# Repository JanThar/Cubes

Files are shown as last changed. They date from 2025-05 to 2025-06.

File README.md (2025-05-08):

- scad datei allgemeine datei. Wenn man di folgenden Sachen auf 1 setz kriegt man ne Aubauvorschau
  // Show lasercutted housing [0,1]
  showWall = 0;
  // Show lasercutted mechanics [0,1]
  showMechanics = 0;
  // Show 3D-printed parts [0,1]
  showPrint = 0;
  // Show axis and motors [0,1]
  showDrive = 0;
  // Show electronics [0,1]
  showElectronic = 0;
  bzw. mit // Flatten for lasercutting [0,1] flatten = 1;
  projection(cut = false) mechanics();
  oder
  projection(cut = false) walls();
  die Laserdateien und unter // 3D-printed die einzelnen 3D-Druckdateien
- svg für den laser, bei der Mechanics datei die z-achse platte und zahnstangen
  (links, zweite/dritte/vierte von oben) nicht cutten, wird vermutlich durch 3D druck ersetzt.
-  stl dateien zum drucken, Anzahl am Ende des Namens. Die 3 Toolhalter (Mill, Penholder, Laser)
  müssen noch mal überarbeitet werden (und dann zusammen mit z-Achsenplatte und Zahnstangen)

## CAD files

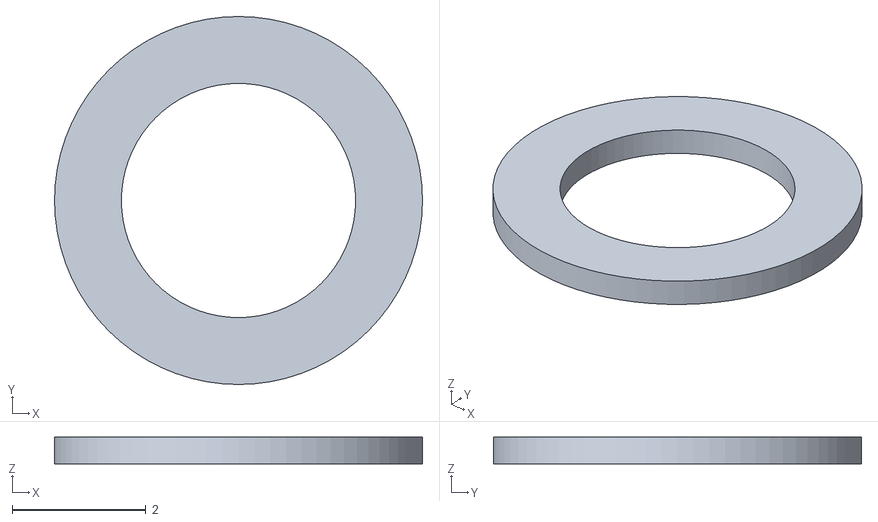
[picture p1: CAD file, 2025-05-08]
unterleg_2.stl
5.50 x 5.50 x 0.4

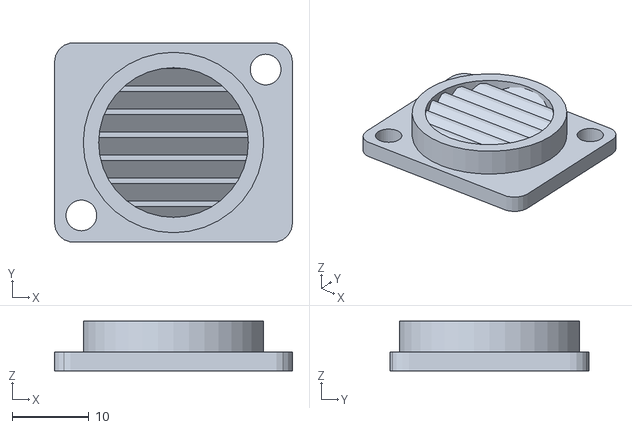
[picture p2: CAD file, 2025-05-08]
neutrixvent_1.stl
31.0 x 25.9 x 6.50

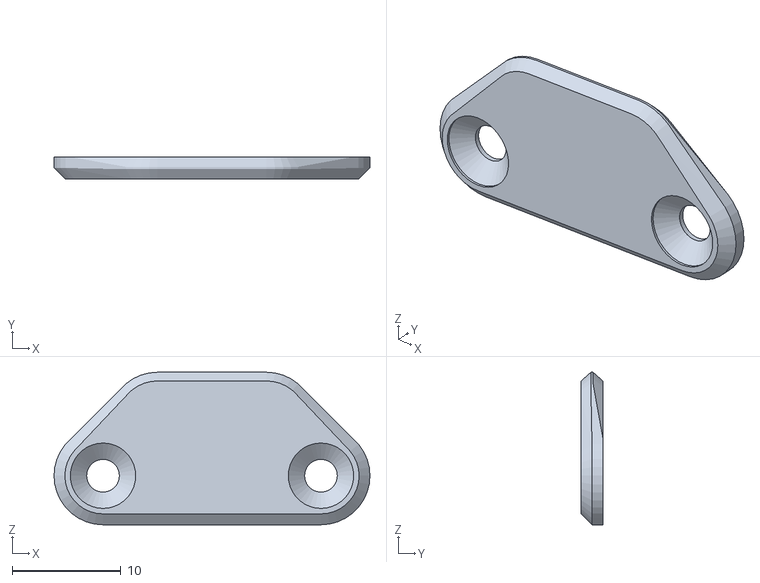
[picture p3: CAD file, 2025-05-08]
doorHandle_1.stl
29.0 x 2.00 x 14.0

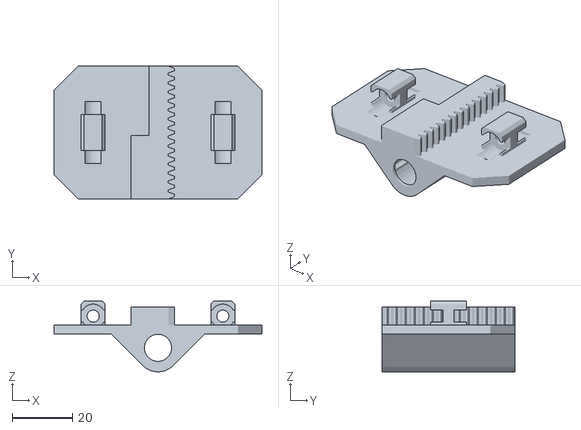
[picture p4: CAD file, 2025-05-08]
PenHolder_1_toMod.stl
69.0 x 44.0 x 23.5

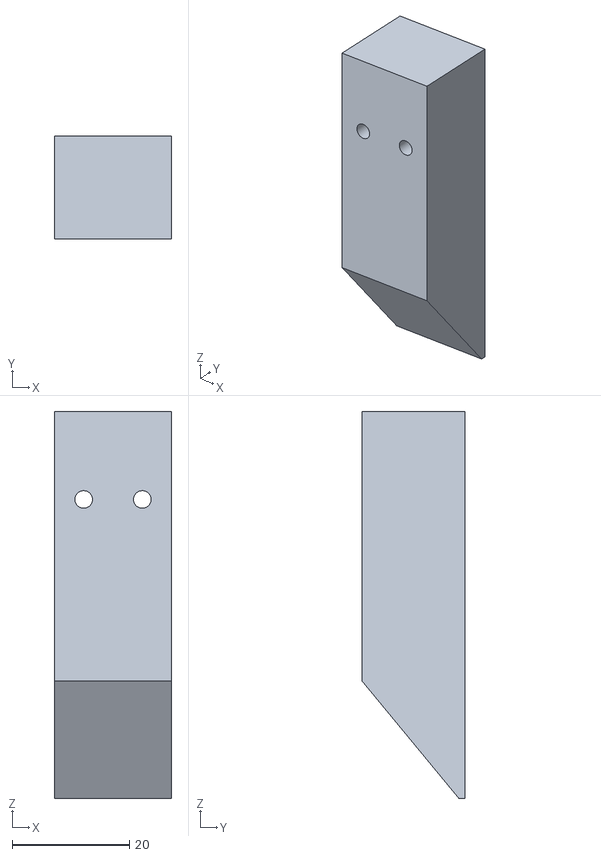
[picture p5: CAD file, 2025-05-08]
Laser_1_toMod.stl
20.0 x 17.5 x 66.0

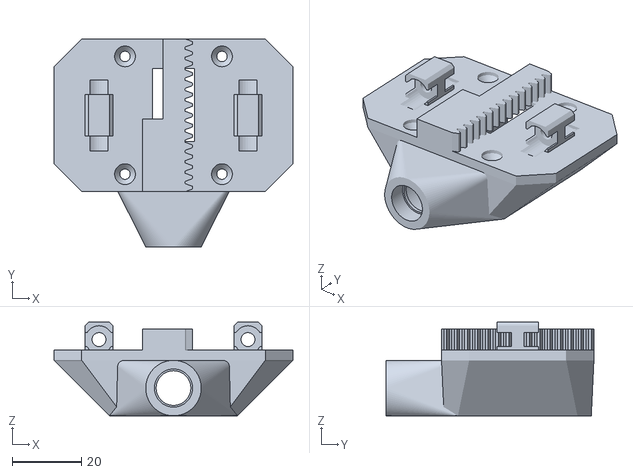
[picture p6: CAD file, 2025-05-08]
Mill_1_toMod.stl
69.0 x 60.0 x 27.0

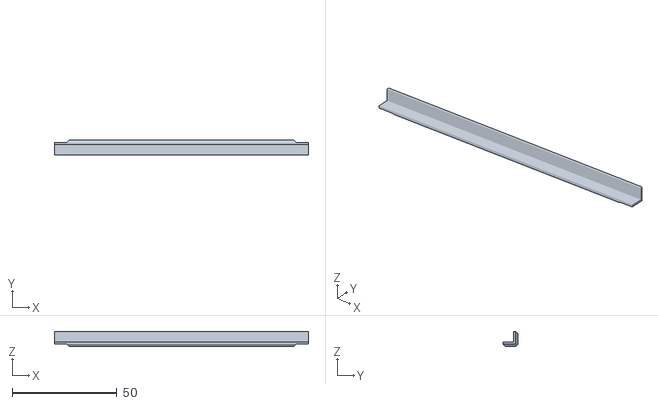
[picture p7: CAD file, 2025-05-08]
coverSide_12.stl
121.1 x 7.00 x 7.00

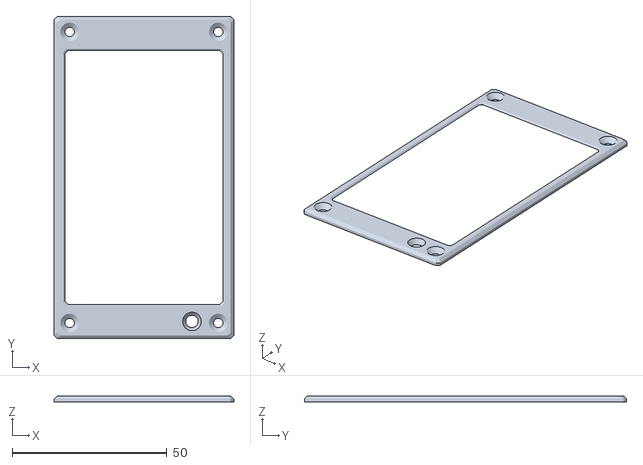
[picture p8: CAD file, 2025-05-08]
screenCover_1.stl
58.0 x 104.0 x 2.00

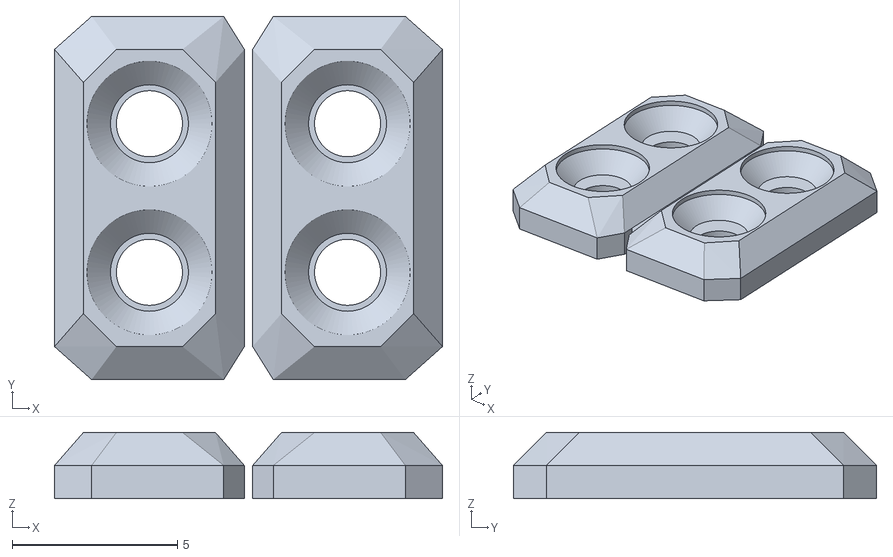
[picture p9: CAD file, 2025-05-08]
HingeA_2_comboDruck.stl
11.8 x 11.0 x 2.00

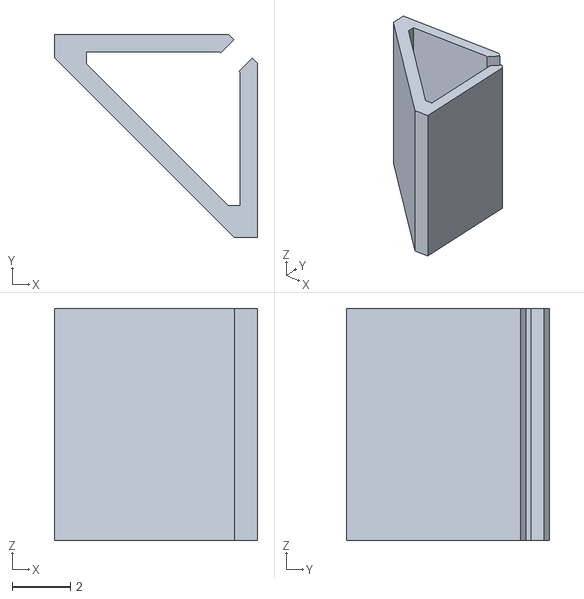
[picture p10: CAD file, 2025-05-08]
CableClip_10.stl
7.00 x 7.00 x 8.00

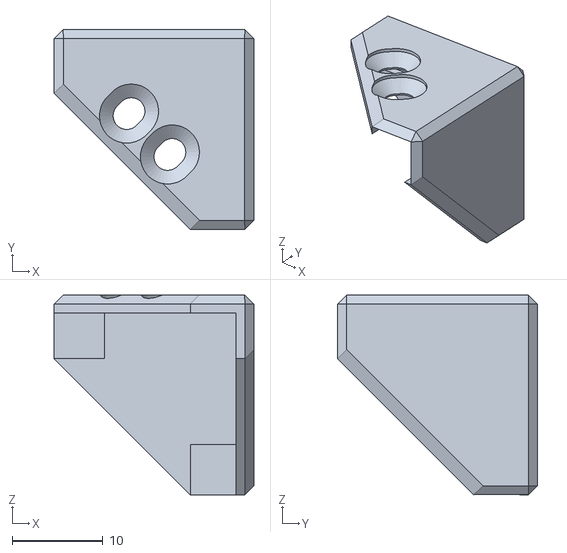
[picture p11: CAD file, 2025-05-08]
coverEdge_8.stl
22.0 x 22.0 x 22.0

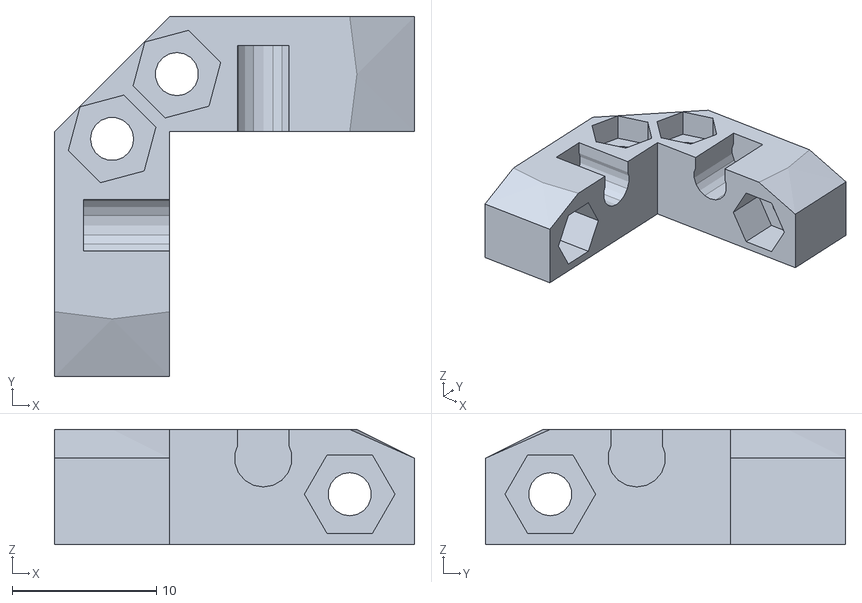
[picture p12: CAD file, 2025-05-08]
connector_30.stl
25.0 x 25.0 x 8.00

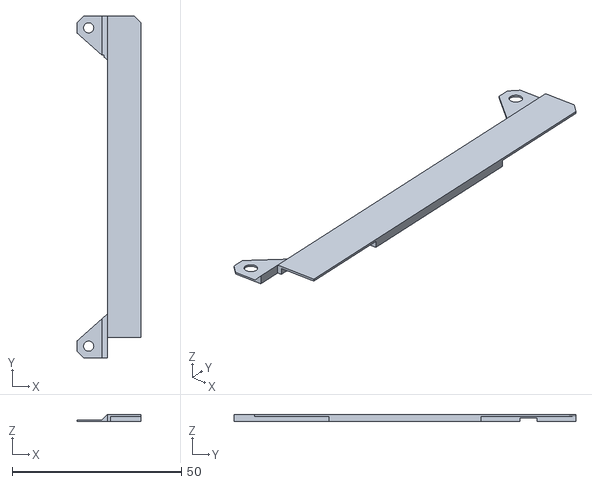
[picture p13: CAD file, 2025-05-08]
LEDHolder_1.stl
19.0 x 101.0 x 2.00

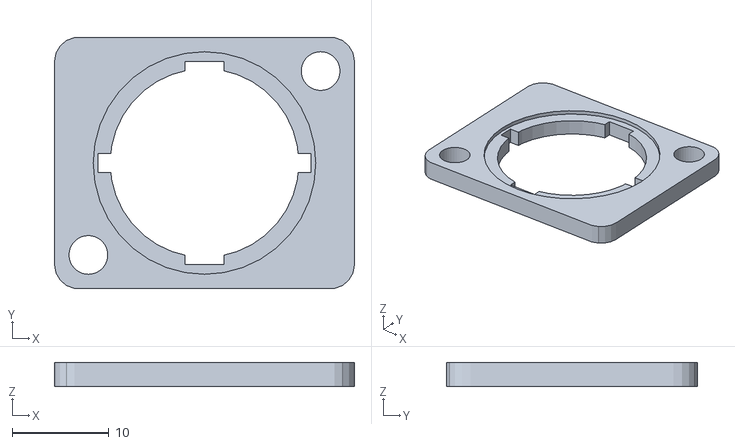
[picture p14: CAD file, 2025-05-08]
neutrixSwitch_1.stl
31.0 x 25.9 x 2.50

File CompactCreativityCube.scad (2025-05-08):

use <Getriebe.scad>

// Nur 1 Schlüsselschalter, 1 Einschalter, 2-4 Motoren!!

// ToDo 
// Türschalter: druck ausreichend??? - Position (Überlappung Neutrix)
// Tür breiter Türrahmen dünner,aussen????, scharnier durchgehend, M3
// da achse vor schlitz eventuell doch aussenrahmen (Griff/Scharnier Combo?????)

// 5 wg iMac, 3 oder 6 wegen Basisform (gelb,rot,blau,grün,lila)
// Printe/Holzmagnet:          120*4*1,5       (Laser) (Printen)
// Businesscard/Stroopwaffel:    85x55x3         (Mill) 
// Keks/Legofliese/Tattoofolie: 15.8x15.8x3.2   (Plotter)
// Marzipan                         (3D Printer)
// Sticker:                         (Cutter)
// Peppers Ghost,Waffel, Schokolade (Tiefziehen) (+Schokoladenbrunnen)
//                                  (Sticken)
// Ringegravierer??
//
// -> Aachen,Holland, Belgien als 3Eck 
//      -> !Printe,Brezel
//      -> !Belgische Waffel, Butter Crisps Blätterteigpastetchen,Pralinen,Spekulatius, Snowball
//      -> !Stroopwafels,Poffertjes

// change connector postion holes top/bottom - nuts to close to axis. add 2 instead 1

// 3D-printed stuff

// move Platform (x-Axis) [-37:37] 
positionX = -37+6;//37-25; //37-24-50
// move Tool (x-Axis) [-37:37]
positionY = 30;
// move Tool (x-Axis) [-15:15] 
positionZ = -15;//11;

// open Door [0:47]
doorAngle = 0;

// Toolhead: 0 unused, 1 Laser, 2 Mill, 3 PrintHead, 4 Pen
useTool = 4; 

toolLaser = 1;
toolMill = 2;
toolPrinter = 3;
toolPen = 4;

//gear inlay laser offset
gearAxisX = 0.12;
gearAxisY = 0.15;
gearLin   = 0.5;

//--------------------------------

positionPiOffsetX = 41;
positionPiOffsetY = 15;

// Flatten for lasercutting [0,1]
flatten = 0;
//projection(cut = false) mechanics();
//projection(cut = false) walls();

// 3D-printed 
//ledholder();
//cableClip(8);
//millInlay();
//millHolder();
//screwHead(1);
penHolder();
//cover();
//bumper();
//hingeTPU(0);
//hingePLA(0);
//doorhandle();
//screenholder(0);
//connector(0);
//vent(0);
//usbA(0);
//usbBack(0);
//keySwitch(0);
//switch(0);
//laserholder();
//wallXside(1,-1,12);

// not used anymore
//led(0);
//frameScreen(); 
//ledFrame(); 

simplifyVent=1;

explodeModules = 0;
explodeAxis = 0;
explodeHousing = 0;

printOffset = 1;//rechter Dremel : Scale 103% printOffset 1.1 (etwas zu gross) 1.05 ok

//animate
//explodeModules = 30*(1-checkA($t*3));
//explodeAxis = 150*(1-checkA($t*3-1));
//explodeHousing = 250*(1-checkA($t*3-1.8));

// Show lasercutted housing [0,1]
showWall = 0;
// Show lasercutted mechanics [0,1]
showMechanics = 0;
// Show 3D-printed parts [0,1]
showPrint = 0;
// Show axis and motors [0,1]
showDrive = 0;
// Show electronics [0,1]
showElectronic = 0;

//--------------------------------

// Dimension y
width = 144;
// Dimension x
length = 144;
// Dimension z
height = 144;
// Height z-Axis
zHeight = 75; //old: 66, new 72 bzw. 75
// Width x-Axis
xWidth = length;

// outer hull - measure for real values
hullWidth  = 150;
hullLength = 150;
hullHeight = 150;

// 139 - 139 - 67

// material thickness for lasercutted parts
materialThickness = 3;
housingThickness = 3;

penWidth = 14; // can be reduced to 12

// distance motor to border
motorDistance = 10;
// distance connectors to border
conDistance = 6;

// screw parameter
screwDiameter = 3;
screwNutDiameter = 6.3;
screwNutHeight = 2.6;
screwLength = 10;

// axis and Bearings
axisHeight = 6; //16;
axisDiameter = 4;
axisShorting = 4;
bearingDiameter = 8;
bearingLength = 8;
offsetBearing = 2.5;

// Connectors 3D-printed
conWidth = 8;
conLength = 17;
conHeight = axisHeight+axisDiameter/2;
conScrewHeight = 10;
conScrewDistance = 5;

// positions
distanceXtoBottom = 20-explodeAxis;
distanceXtoBack = 0;
distanceYtoBottom = -zHeight/2+height-conHeight*2;
distanceYtoBack = -(width/2-20)+explodeAxis;
distanceZtoBottom = distanceYtoBottom+explodeAxis;
distanceZtoBack = distanceYtoBack+32-explodeAxis;

// door parameter
doorRounding = 10;
doorOverlap = 3;
doorHeight = height-conHeight*2-distanceXtoBottom+materialThickness-15;
doorWidth = 124;
doorExtensionX = 0;
doorDistanceToBottom = distanceXtoBottom+conHeight+materialThickness+3;

//define variables to identfy axis
x=0;
y=1;
z=2;

//Animation
function checkA(a)=(checkB((a>1)?1:a));
function checkB(a)=((a<0)?0:a);

//--------------------------------

//                translate([0,-130,10]) //screen
//rotate([-70,0,0])
//                    cube([85.5,20,55],true);

//electronic
if(showElectronic) {
//    translate([length/2-positionPiOffsetX,-width/2+positionPiOffsetY,18.5]) rotate([0,180,180]) piZero(0);
    //color("green") translate([-29-8,0,10]) cube([76,121,10],center=true); // 5 inch display
}

//toolhead
if(showDrive) translate([-positionY,0,positionZ+explodeAxis]) {
    if (useTool==toolLaser) 
        translate([0,3,86-3]) {
            laser(0); // 10-100 mm Focus
            laserholder();
        }
    if (useTool==toolPen) 
        translate([0,0,86-3]) {
            //laser(0); // 10-100 mm Focus
            penHolder();
        }
    if (useTool==toolMill) 
        translate([0,-3.7,distanceZtoBottom+5]) 
        mill(); 
    if (useTool==toolPrinter) 
        translate([-6,-13-5,73+45.5-6]) 
        printhead(); 
}

//walls
if (showWall) walls();
    
//mechanic
if (showMechanics)  mechanics();
    
module cableClip(clipLength) {
    difference() {
        hull() {
            translate([0,conHeight/2-0.4,0])
                cube([conHeight-2,0.8,clipLength],true);
            translate([conHeight/2-0.4,0,0])
                cube([0.8,conHeight-2,clipLength],true);
        }
        hull() {
            translate([0.4,conHeight/2-0.4-0.4,0])
                cube([conHeight-3.4,0.4,clipLength*2],true);
            translate([conHeight/2-0.4-0.4,0.4,0])
                cube([0.4,conHeight-3.4,clipLength*2],true);
        }
        translate([3,3,0])
            rotate([0,0,-45])
            cube([0.9,conHeight-3.4,clipLength*2],true);
    }
}
    
module bumpers() {
    for(i=[0:3])
        rotate([0,0,90*i])
        bumper();
    
    for(i=[0:3])
        translate([0,0,height])
        rotate([180,0,90*i])
        bumper();
}    
module covers() {
for(i=[0:4])
    rotate([0,0,90*i])
    translate([0,0,(hullWidth-6)/2])
    rotate([0,90,0])
    cover();
translate([0,0,(hullWidth-6)/2])
    for(i=[0:4])
    rotate([90*i,0,0])
    cover();
translate([0,0,(hullWidth-6)/2])
    for(i=[0:4])
    rotate([90*i,0,90])
    cover();
}
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

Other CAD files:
neutrixUSB_A_1.stl
DoorFrame_1.stl
neutrixKey_1.stl
MillInlay_1.stl
HingeB_2_comboDruck.stl
neutrixUSB_Back_1.stl

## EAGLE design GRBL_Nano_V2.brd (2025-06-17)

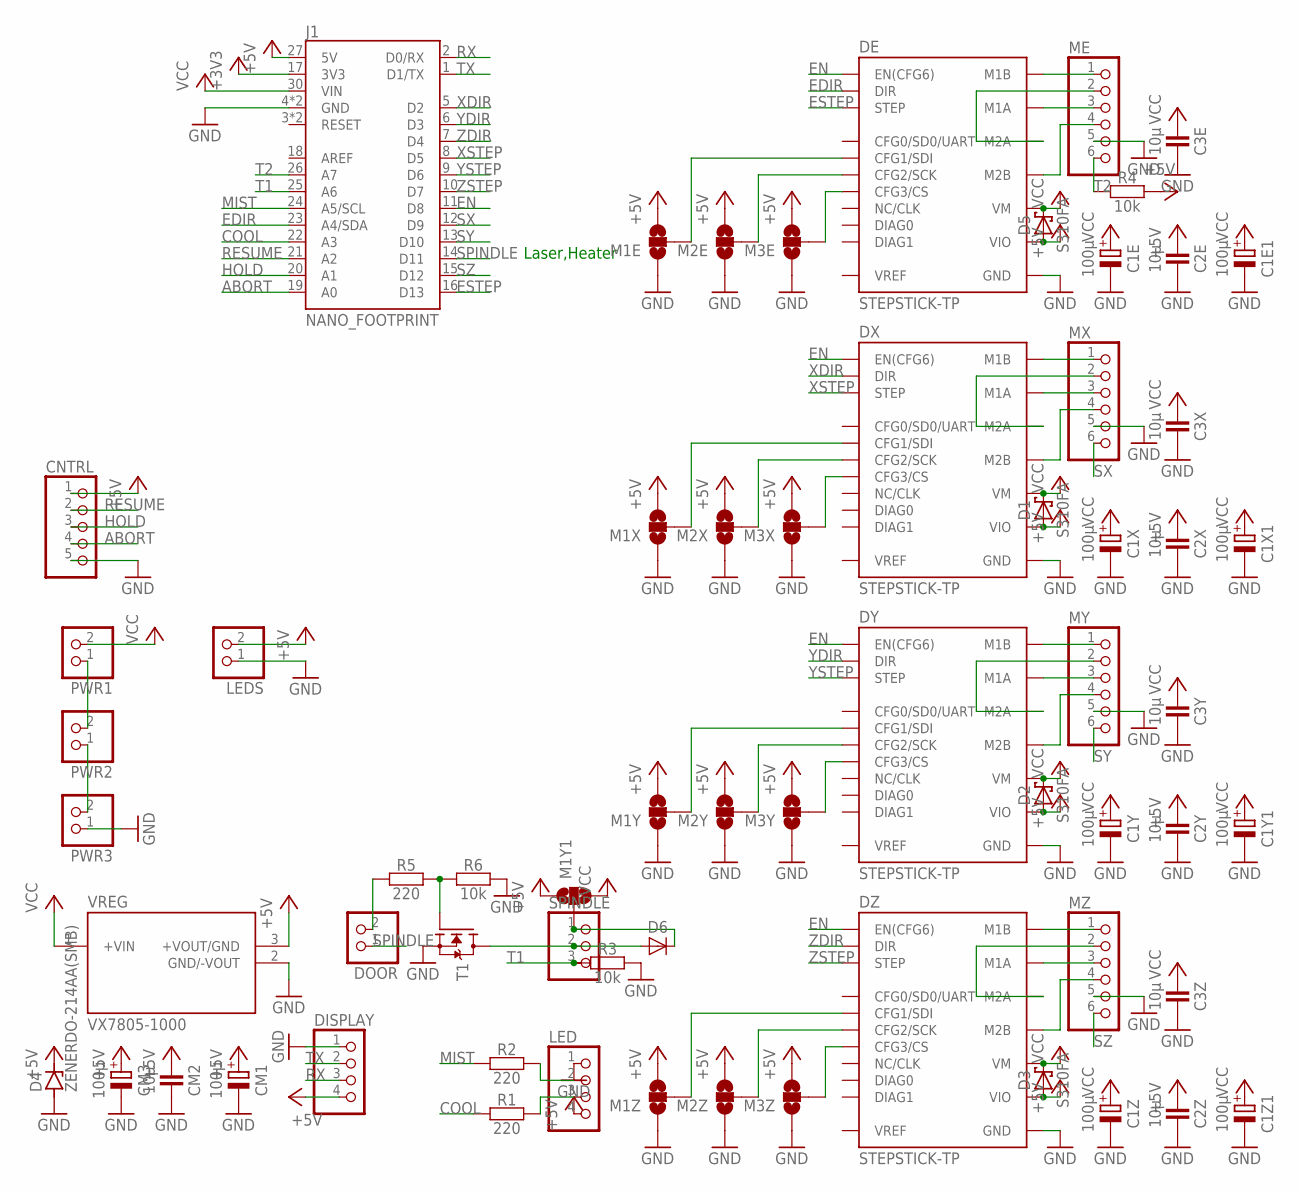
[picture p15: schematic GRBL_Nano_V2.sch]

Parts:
C1E, C1X, C1Y, C1Z: 100µ; C_8MM
C1E1, C1X1, C1Y1, C1Z1: 100µ; C_E5-10
C2E, C2X, C2Y, C2Z, C3E, C3X, C3Y, C3Z: 10µ; C0805
CM1: 100µ; C_8MM
CM2: 10µ; C0805
CM3: 100µ; C_E5-10
CNTRL: PINHD-1X5; 1X05
D1, D2, D3, D5: S310FA; SOD123
D4: ZENERDO-214AA(SMB); DIOM5336X265N
D6: DIODE-SMA; SMA_DO214AC
DE: STEPSTICK-TP; SSS_TP
DISPLAY: PINHD-1X4; 1X04
DOOR: PINHD-1X2; 1X02
DX: STEPSTICK-TP; SSS_TP
DY: STEPSTICK-TP; SSS_TP
DZ: STEPSTICK-TP; SSS_TP
J1: NANO_FOOTPRINT; NANO
LED: PINHD-1X4; 1X04
LEDS: PINHD-1X2; 1X02
M1E, M1X, M1Y, M1Y1, M1Z, M2E, M2X, M2Y, M2Z, M3E, M3X, M3Y, M3Z: SOLDERJUMPER_2WAY-OLDS; SJ_3
ME: PINHD-1X6; 1X06
MX: PINHD-1X6; 1X06
MY: PINHD-1X6; 1X06
MZ: PINHD-1X6; 1X06
PWR1, PWR2, PWR3: PINHD-1X2; 1X02
R1, R2, R5: 220; C0805
R3, R4, R6: 10k; C0805
SPINDLE: PINHD-1X3; 1X03
T1: MOSFET-N-DPAK; DPAK_TO252
VREG: VX7805-1000; VX78012-1000_VX7805-1000

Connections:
+3V3: J1.17 (3V3)
+5V: C2E.1, C2X.1, C2Y.1, C2Z.1, CM1.+, CM2.1, CM3.+, CNTRL.1, D1.A, D2.A, D3.A, D4.2 (C), D5.A, DE.VIO, DISPLAY.4, DX.VIO, DY.VIO, DZ.VIO, J1.27 (5V), LED.4, LEDS.2, M1E.3, M1X.3, M1Y.3, M1Y1.1, M1Z.3, M2E.3, M2X.3, M2Y.3, M2Z.3, M3E.3, M3X.3, M3Y.3, M3Z.3, R4.2, VREG.3 (+VOUT/GND)
ABORT: CNTRL.4, J1.19 (A0)
COOL: J1.22 (A3), R1.1
COOL1: LED.3, R1.2
EDIR: DE.DIR, J1.23 (A4/SDA)
EN: DE.EN (EN(CFG6)), DX.EN (EN(CFG6)), DY.EN (EN(CFG6)), DZ.EN (EN(CFG6)), J1.11 (D8)
ESTEP: DE.STEP, J1.16 (D13)
GND: C1E.-, C1E1.-, C1X.-, C1X1.-, C1Y.-, C1Y1.-, C1Z.-, C1Z1.-, C2E.2, C2X.2, C2Y.2, C2Z.2, C3E.2, C3X.2, C3Y.2, C3Z.2, CM1.-, CM2.2, CM3.-, CNTRL.5, D4.1 (A), DE.GND@1 (GND), DE.GND@2 (GND), DISPLAY.1, DX.GND@1 (GND), DX.GND@2 (GND), DY.GND@1 (GND), DY.GND@2 (GND), DZ.GND@1 (GND), DZ.GND@2 (GND), J1.4 (GND), J1.29 (GND), LED.1, LEDS.1, M1E.1, M1X.1, M1Y.1, M1Z.1, M2E.1, M2X.1, M2Y.1, M2Z.1, M3E.1, M3X.1, M3Y.1, M3Z.1, ME.5, MX.5, MY.5, MZ.5, PWR3.1, R3.2, R6.2, T1.3 (S), VREG.2 (GND/-VOUT)
HOLD: CNTRL.3, J1.20 (A1)
MIST: J1.24 (A5/SCL), R2.1
MIST1: LED.2, R2.2
unnamed: DX.M1A, MX.3
unnamed: DX.M2B, MX.4
unnamed: DX.M2A, MX.2
unnamed: DX.M1B, MX.1
unnamed: DZ.M1B, MZ.1
unnamed: DZ.M1A, MZ.3
unnamed: DY.M1B, MY.1
unnamed: DY.M1A, MY.3
unnamed: DY.M2A, MY.2
unnamed: DZ.M2A, MZ.2
unnamed: DZ.M2B, MZ.4
unnamed: DY.M2B, MY.4
unnamed: D6.A, SPINDLE.2, T1.2 (D)
unnamed: DOOR.2, R5.1
unnamed: DX.CFG1 (CFG1/SDI), M1X.2
unnamed: DX.CFG2 (CFG2/SCK), M2X.2
unnamed: DX.CFG3 (CFG3/CS), M3X.2
unnamed: DY.CFG1 (CFG1/SDI), M1Y.2
unnamed: DY.CFG2 (CFG2/SCK), M2Y.2
unnamed: DY.CFG3 (CFG3/CS), M3Y.2
unnamed: DZ.CFG1 (CFG1/SDI), M1Z.2
unnamed: DZ.CFG2 (CFG2/SCK), M2Z.2
unnamed: DZ.CFG3 (CFG3/CS), M3Z.2
unnamed: DE.M2B, ME.4
unnamed: DE.M1B, ME.1
unnamed: PWR1.1, PWR2.2
unnamed: D6.C, M1Y1.2, SPINDLE.1
unnamed: PWR2.1, PWR3.2
unnamed: DE.M1A, ME.3
unnamed: DE.M2A, ME.2
unnamed: DE.CFG1 (CFG1/SDI), M1E.2
unnamed: DE.CFG2 (CFG2/SCK), M2E.2
unnamed: DE.CFG3 (CFG3/CS), M3E.2
unnamed: R5.2, R6.1, T1.1 (G)
RESUME: CNTRL.2, J1.21 (A2)
RX: DISPLAY.3, J1.2 (D0/RX)
SPINDLE: DOOR.1, J1.14 (D11)
SX: J1.12 (D9), MX.6
SY: J1.13 (D10), MY.6
SZ: J1.15 (D12), MZ.6
T1: J1.25 (A6), R3.1, SPINDLE.3
T2: J1.26 (A7), ME.6, R4.1
TX: DISPLAY.2, J1.1 (D1/TX)
VCC: C1E.+, C1E1.+, C1X.+, C1X1.+, C1Y.+, C1Y1.+, C1Z.+, C1Z1.+, C3E.1, C3X.1, C3Y.1, C3Z.1, D1.C, D2.C, D3.C, D5.C, DE.VM, DX.VM, DY.VM, DZ.VM, J1.30 (VIN), M1Y1.3, PWR1.2, VREG.1 (+VIN)
XDIR: DX.DIR, J1.5 (D2)
XSTEP: DX.STEP, J1.8 (D5)
YDIR: DY.DIR, J1.6 (D3)
YSTEP: DY.STEP, J1.9 (D6)
ZDIR: DZ.DIR, J1.7 (D4)
ZSTEP: DZ.STEP, J1.10 (D7)

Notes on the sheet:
Laser,Heater

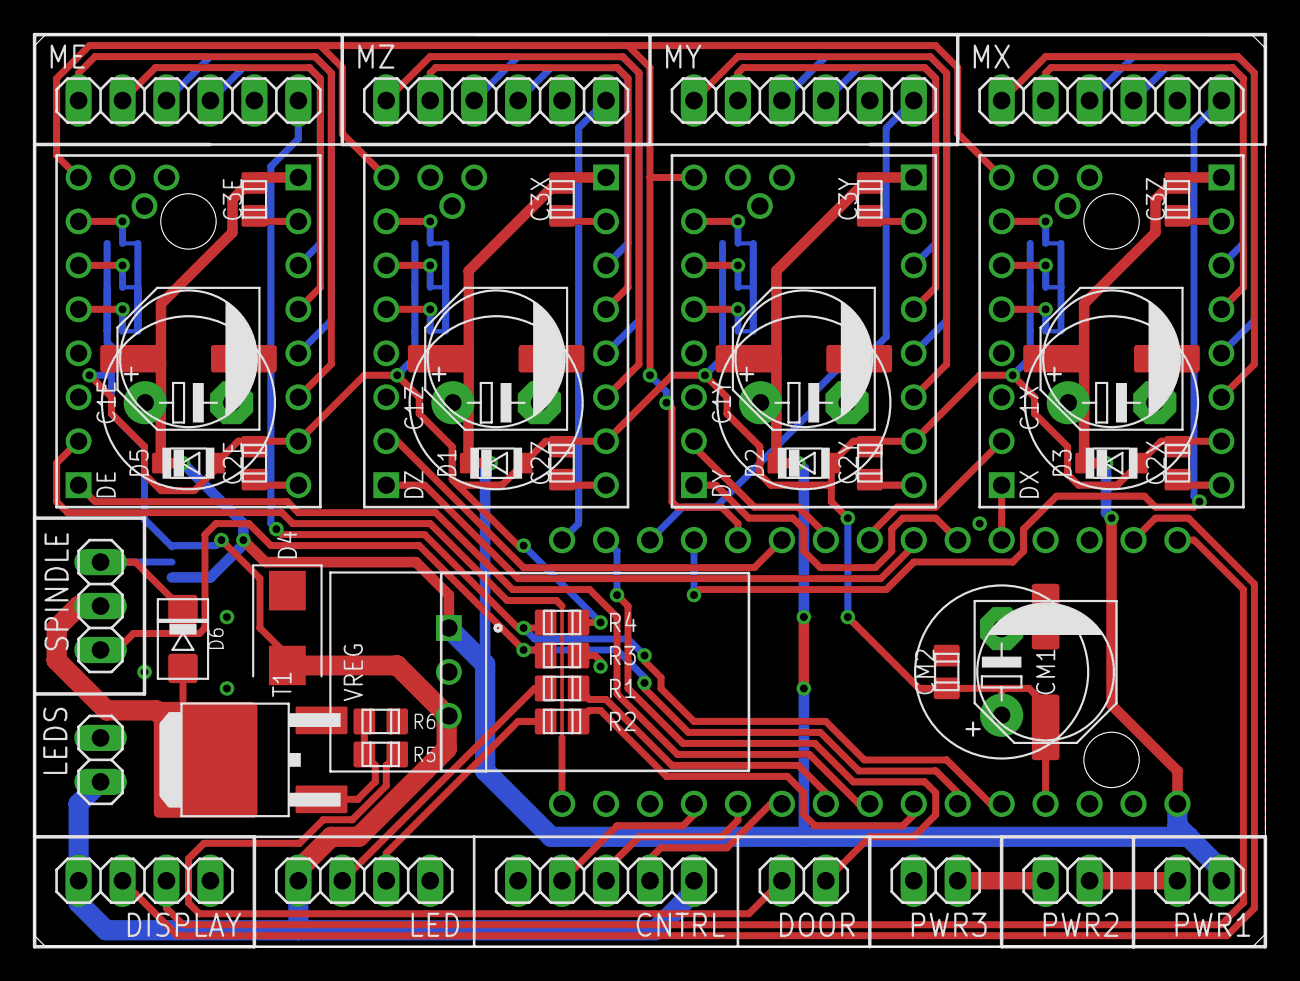
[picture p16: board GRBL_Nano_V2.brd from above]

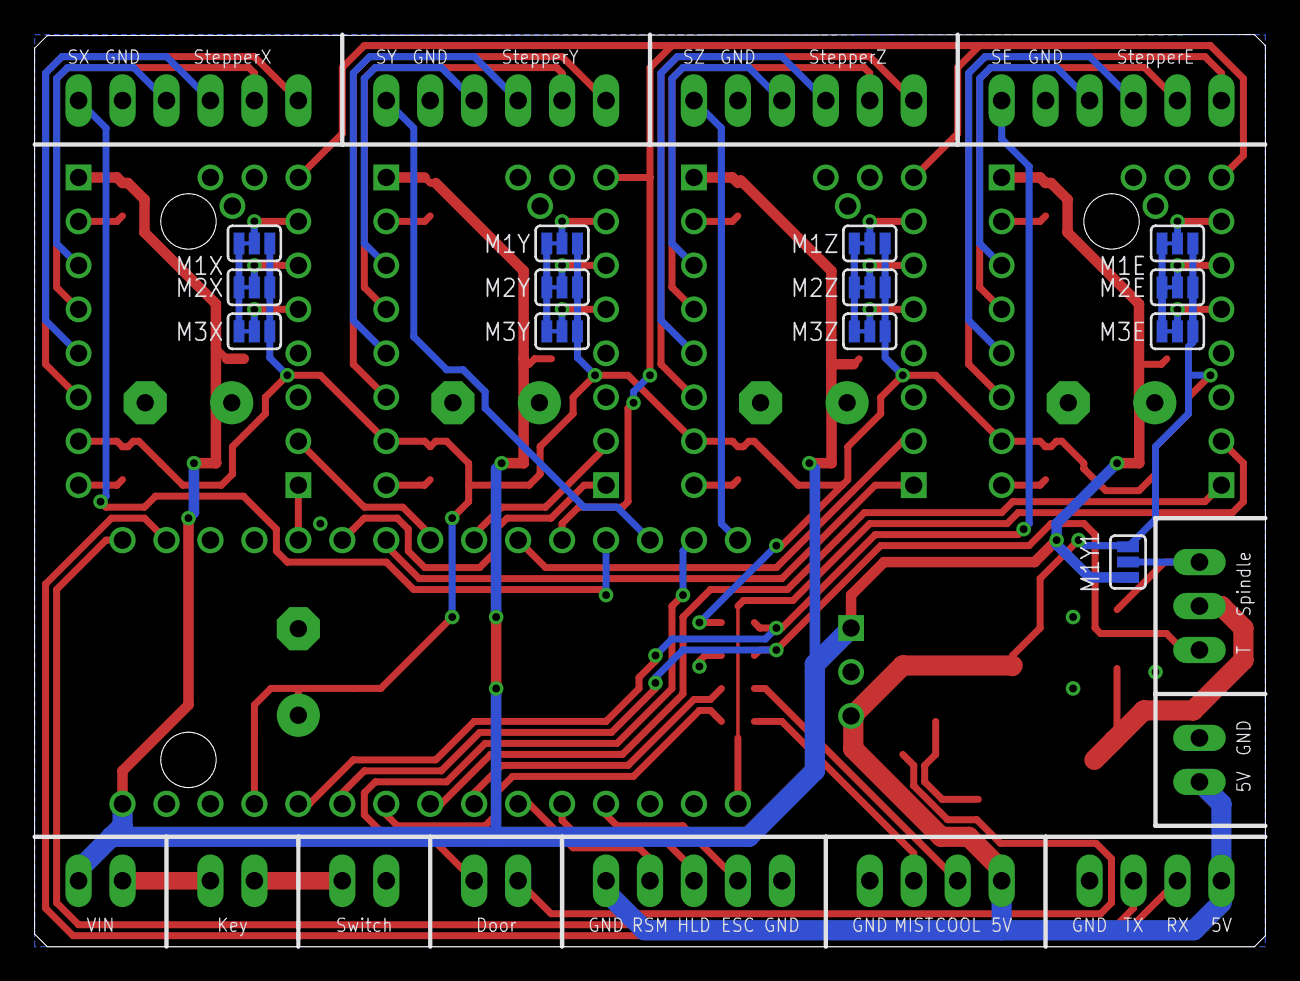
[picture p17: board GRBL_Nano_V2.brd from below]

Board: 2 copper layers, 71.1 x 52.7 mm, 64 parts (13 on the bottom side), 61 nets.

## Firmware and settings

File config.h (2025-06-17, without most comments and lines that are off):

#define config_h
#include "grbl.h" // For Arduino IDE compatibility.
#define DEFAULTS_GENERIC
#define BAUD_RATE 115200
#define CPU_MAP_ATMEGA328P // Arduino Uno CPU
#define CMD_STATUS_REPORT '?'
#define CMD_FEED_HOLD '!'
#define CMD_CYCLE_START '~'
#define CMD_RESET 0x18 // ctrl-x.
#define CMD_SAFETY_DOOR '@'
#define HOMING_INIT_LOCK // Comment to disable
#define HOMING_CYCLE_0 (1<<Z_AXIS)                // REQUIRED: First move Z to clear workspace.
#define HOMING_CYCLE_1 (1<<Y_AXIS)  // OPTIONAL: Then move X,Y at the same time.
#define HOMING_CYCLE_2 (1<<X_AXIS)                  // OPTIONAL: Uncomment and add axes mask to enable
#define N_HOMING_LOCATE_CYCLE 1 // Integer (1-128)
#define N_STARTUP_LINE 2 // Integer (1-2)
#define N_DECIMAL_COORDVALUE_INCH 4 // Coordinate or position value in inches
#define N_DECIMAL_COORDVALUE_MM   3 // Coordinate or position value in mm
#define N_DECIMAL_RATEVALUE_INCH  1 // Rate or velocity value in in/min
#define N_DECIMAL_RATEVALUE_MM    0 // Rate or velocity value in mm/min
#define N_DECIMAL_SETTINGVALUE    3 // Decimals for floating point setting values
#define MESSAGE_PROBE_COORDINATES // Enabled by default. Comment to disable.
#define SAFETY_DOOR_SPINDLE_DELAY 4000
#define SAFETY_DOOR_COOLANT_DELAY 1000
#define ACCELERATION_TICKS_PER_SECOND 100
#define ADAPTIVE_MULTI_AXIS_STEP_SMOOTHING  // Default enabled. Comment to disable.
#define TOOL_LENGTH_OFFSET_AXIS Z_AXIS // Default z-axis. Valid values are X_AXIS, Y_AXIS, or Z_AXIS.
#define VARIABLE_SPINDLE // Default enabled. Comment to disable.
#define SPINDLE_MAX_RPM 1000.0 // Max spindle RPM. This value is equal to 100% duty cycle on the PWM.
#define SPINDLE_MIN_RPM 0.0    // Min spindle RPM. This value is equal to (1/256) duty cycle on the PWM.
#define MINIMUM_JUNCTION_SPEED 0.0 // (mm/min)
#define MINIMUM_FEED_RATE 1.0 // (mm/min)
#define N_ARC_CORRECTION 12 // Integer (1-255)
#define ARC_ANGULAR_TRAVEL_EPSILON 5E-7 // Float (radians)
#define DWELL_TIME_STEP 50 // Integer (1-255) (milliseconds)
#if defined(USE_SPINDLE_DIR_AS_ENABLE_PIN) && !defined(VARIABLE_SPINDLE)
  #error "USE_SPINDLE_DIR_AS_ENABLE_PIN may only be used with VARIABLE_SPINDLE enabled"
#endif
#if defined(USE_SPINDLE_DIR_AS_ENABLE_PIN) && !defined(CPU_MAP_ATMEGA328P)
  #error "USE_SPINDLE_DIR_AS_ENABLE_PIN may only be used with a 328p processor"
#endif

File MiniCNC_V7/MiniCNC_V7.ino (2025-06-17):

//Pinout ESP32-3248S035
// LED onboard: Blue-IO17, Red-IO4, Green-IO16  -> replace status LED on front
// Photoresistor: IO34
// Speaker: V01,V02 - IO26
// SD DAT2-3.3V,CD-IO5, CMD/MOSI-IO23,VDD-3.3V,CLX/CLK-IO18,VSS-GND,DAT0/MISO-IO19,DAT1-??,CD-?? -> Data storage (images)
// I2C
// 4Pin VIN,TX-IO1,RX-IO3,GND Serial            -> GRBL sender, power supply
// TPC???
// 4Pin GND/NC/IO21/3.3V Temp&Humidity???       -> 
// 4Pin GND/IO35/IO22/IO21 Extended IO          -> check door?? check housing??
// Display IO27 LED, CLK-IO14, MISO-IO12, MOSI-IO13, CS-IO15, RS-IO2
// Flash IO6, IO7, IO8, IO9, IO10, IO11         -> alternative for data storage, unpopulated
// Touch SDA-IO33,SCL-32,IRQ-IO36,RST-IO25
// !! (missing) 5V led strip (white) - solder directly at Serial or pads S3/S1 (or LED driver)

// BMP und GCODE parallel auf SD-Karte, gleicher Name, andere Endung


// LED pinout
#define LED_RED    4
#define LED_GREEN 16
#define LED_BLUE  17

// Bluetooth
#include "BluetoothSerial.h"

#if !defined(CONFIG_BT_ENABLED) || !defined(CONFIG_BLUEDROID_ENABLED)
#error Bluetooth is not enabled! Please run `make menuconfig` to and enable it
#endif

BluetoothSerial SerialBT;
String deviceName = "CubeLASER";
int BTconfirmed = 0;

// Tft
#include <SPI.h>
#include <TFT_eSPI.h>
TFT_eSPI tft = TFT_eSPI(320,480);

#include "VeraMono17pt7b.h"
#define TEXTOFFSET 20
#define TEXTSIZESMALL 1
#define TEXTSIZEBIG 1

// Touch
#include "TouchDrvGT911.hpp"
#define SENSOR_SDA  33
#define SENSOR_SCL  32
#define SENSOR_IRQ  36
#define SENSOR_RST  25

TouchDrvGT911 touch;
int16_t touchX[5], touchY[5];

//  SD CARD
#include "FS.h"
#include "SD.h"
#include "SPI.h"

#define SPI_SCK 18
#define SPI_MISO 19
#define SPI_MOSI 23
#define SPI_SS_SD 5

void init_sd();
void listDir(fs::FS &fs, const char * dirname, uint8_t levels);

File myDesigns;

char namebuf[32] = "/";   //BMP files in root directory

// screen stuff

#include "bitmaps.h"
#include "letters.h"
#include "screens.h"

#define MINPRESSURE 200
#define MAXPRESSURE 1000

#define NAMEMATCH ""         // "" matches any name
#define PALETTEDEPTH   8     // support 256-colour Palette

bool debug = true;
bool GRBLactive = false;

int txtPos = 0;
int txtIndex = 0;
int txtMaxLength = 10;

int imgIndex = 0;

int pageIndex = 0;

int txtBuf[30];

String fileNameBMP, fileNameNC;

TFT_eSPI_Button keypad[3][10];
TFT_eSPI_Button imageBTN;
TFT_eSPI_Button okBTN;
TFT_eSPI_Button backBTN;
char keyChar[30] = {  // Only Uppercase
  'Q', 'W', 'E', 'R', 'T', 'Y', 'U', 'I', 'O', 'P',
  'A', 'S', 'D', 'F', 'G', 'H', 'J', 'K', 'L', '-',
  'Z', 'X', 'C', 'V', 'B', 'N', 'M', '@', '#', ' '
};

String allLetters = "QWERTYUIOPASDFGHJKL-ZXCVBNM@# ";
char theLetter = allLetters.charAt(0);

String Test = "Hallo";
int pixel_x, pixel_y;  //Touch_getXY() updates global vars

#define BLACK 0x0000
#define BLUE 0x001F
#define RED 0xF800
#define GREEN 0x07E0
#define CYAN 0x07FF
#define MAGENTA 0xF81F
#define YELLOW 0xFFE0
#define WHITE 0xFFFF
#define GREY 0x39E7

bool Touch_getXY(void) {
  uint8_t touched = touch.getPoint(touchX, touchY, touch.getSupportTouchPoint());
  if (touched > 0) {
    pixel_x = touchY[0];
    pixel_y = 320-touchX[0];
    if(debug) {
      //Serial.print(millis());
      //Serial.print("ms ");
      //for (int i = 0; i < touched; ++i) {
        Serial.print("X: ");
        Serial.print(pixel_x);
        Serial.print(" ,Y: ");
        Serial.println(pixel_y);
        //Serial.print(" ,Pressed: ");
        //Serial.println(touched > 0);
        //tft.fillRect(touchY[0], 320-touchX[0], 5, 5, RED);
      //}
    }
    return true;
  }
  return false;
}

//  SD CARD
//  ==========================================
void init_sd() {
  if(!SD.begin(SS)){
    SPIClass spi = SPIClass(VSPI);
    if(!SD.begin(SS, spi, 80000000))
      Serial.println("Card Mount Failed");
    return;
  }
  uint8_t cardType = SD.cardType();

  if(cardType == CARD_NONE){
    Serial.println("No SD card attached");
    return;
  }

  Serial.print("SD Card Type: ");
  if(cardType == CARD_MMC){
    Serial.println("MMC");
  } else if(cardType == CARD_SD){
    Serial.println("SDSC");
  } else if(cardType == CARD_SDHC){
    Serial.println("SDHC");
  } else {
    Serial.println("UNKNOWN");
  }

  uint64_t cardSize = SD.cardSize() / (1024 * 1024);
  Serial.printf("SD Card Size: %lluMB\n", cardSize);

  listDir(SD, "/", 1);
  Serial.println("------");
  listDir(SD, "/", 1);
}

void listDir(fs::FS &fs, const char * dirname, uint8_t levels){
  Serial.printf("Listing directory: %s\n", dirname);
  try {
    File root = fs.open(dirname);
    if(!root){
      Serial.println("Failed to open directory");
      return;
    }
    if(!root.isDirectory()){
      Serial.println("Not a directory");
      return;
    }

    File file = root.openNextFile();
    while(file){
      if(file.isDirectory()){
        Serial.print("  DIR : ");
       Serial.println(file.name());
        if(levels){
          listDir(fs, file.name(), levels -1);
        }
      } else {
        Serial.print("  FILE: ");
       Serial.print(file.name());
        Serial.print("  SIZE: ");
        Serial.println(file.size());
      }
      file = root.openNextFile();
    }
    root.close();

  } catch(String error) {
    Serial.println("LS: Oops exception");
  }
  Serial.println("LS: NEXT");
}

void setup(void) { //setup second serial for sending gcode
  pinMode(LED_RED, OUTPUT);
  pinMode(LED_GREEN, OUTPUT);
  pinMode(LED_RED, OUTPUT);
  setStatusLED(0,255,255);
  delay(100);
  setStatusLED(255,255,0);
  delay(100);
  Serial.begin(115200); 

  // Set the default PIN - not working
//  esp_bt_pin_type_t pin_type = ESP_BT_PIN_TYPE_FIXED;
//  esp_bt_pin_code_t pin_code = {'1', '2', '3', '4'}; // Change '1234' to your desired PIN
//  esp_bt_gap_set_pin(pin_type, 4, pin_code);

  SerialBT.begin(deviceName); 
  tft.init();
  tft.setRotation(1);  //PORTRAIT
  tft.setFreeFont(&VeraMono15pt7b);

  // start SD
  init_sd();

  touch.setPins(SENSOR_RST, SENSOR_IRQ);
  if (!touch.begin(Wire, GT911_SLAVE_ADDRESS_L, SENSOR_SDA, SENSOR_SCL)) {
    while (1) {
      Serial.println("Failed to find GT911 - check your wiring!");
      delay(1000);
    }
  }

  Serial.println("Init GT911 Sensor success!");

  // Set the center button to trigger the callback , Only for specific devices, e.g LilyGo-EPD47 S3 GT911
  touch.setHomeButtonCallback([](void *user_data) {
    Serial.println("Home button pressed!");
  }, NULL);

  for (int i = 0; i < 3; i++) {
    for (int j = 0; j < 10; j++) {
      theLetter = allLetters.charAt(i*10+j);//i*10+j
      keypad[i][j].initButton(&tft, 24 + j * 48, 154 + i * 46, 42, 40, WHITE, BLACK, WHITE,&theLetter, TEXTSIZESMALL); 
    }
  }

  initKeyPadButtons();

  imageBTN.initButton(&tft, 128, 62, 70, 112, BLACK, BLACK, WHITE, " ", TEXTSIZESMALL);
  backBTN.initButton(&tft, 336, 296, 90, 40, WHITE, BLACK, WHITE, "<-", TEXTSIZESMALL);
  okBTN.initButton(&tft, 432, 296, 90, 40, WHITE, BLACK, WHITE, "OK", TEXTSIZESMALL);

  if (debug) Serial.println("Startup done");
  setStatusLED(255,0,255);
  initWelcomeScreen();
}

void setStatusLED(int red, int green, int blue) {
  analogWrite(LED_RED, red);
  analogWrite(LED_GREEN, green);
  analogWrite(LED_BLUE, blue);
}

void sendGRBL(const char text[][14], int size) {
  // send command
  for(int j=0;j<size/14;j++) {
    Serial1.println(text[j]);
    Serial1.flush();
    if (debug) Serial.println(text[j]);
    Serial.flush();
  
    //wait for ok
    bool ack = false;
    while(!ack) {
      while (Serial1.available()) {       
       // If anything comes in Serial1 (pins 0 & 1)
       char test = Serial1.read();
       Serial.write(test);
       Serial.flush();
        if (test == 'k') {
          ack = true;
        }
      }
    }
  }
}

void initWelcomeScreen() {
  tft.fillScreen(BLACK);
  tft.drawRoundRect(3, 2, 474, 120, 10, WHITE);
  // Text/Image Printenlaser, Preparations

  okBTN.drawButton(false);

  tft.drawRoundRect(3, 2, 474, 120, 10, WHITE);

  tft.setTextColor(WHITE);
  tft.setTextSize(TEXTSIZEBIG);
  tft.setCursor(180, 20+TEXTOFFSET);
  tft.print(welcometitle[0]);
  tft.setCursor(180, 50+TEXTOFFSET);
  tft.print(welcometitle[1]);
  tft.setCursor(180, 80+TEXTOFFSET);
  tft.print(welcometitle[2]);

  tft.drawBitmap(93, 10, epd_bitmap_allArray[0], 70, 100, WHITE);

  tft.setTextSize(TEXTSIZESMALL);

  for(int i=0;i<(sizeof(startscreen)/40);i++) {
    tft.setCursor(10, 140+i*30+TEXTOFFSET);
    tft.print(startscreen[i]);
  }
  for(int i=0; i<5; i++) {
    tft.setCursor(10, 140+i*30+TEXTOFFSET);
    tft.print(startscreen[i]);
  }
}

void initDesignScreen() {
  tft.fillScreen(BLACK);
  tft.drawRoundRect(3, 2, 474, 120, 10, WHITE);

  drawTextArea();

  imageBTN.drawButton(false);
  drawImageArea();

  for (int i = 0; i < 3; i++) {
    for (int j = 0; j < 10; j++) {
      keypad[i][j].drawButton(false);
    }
  }
  backBTN.drawButton(false);
  okBTN.drawButton(false);
}

void initStartScreen() {
  //Everything ok (Printe, door closed)
  tft.fillRect(3, 122, 474, 150, BLACK);

  tft.setTextSize(TEXTSIZESMALL);
  tft.setTextColor(WHITE);
  for(int i=0; i<5; i++) {
    tft.setCursor(10, 140+i*30+TEXTOFFSET);
    tft.print(initscreen[i]);
  }

  backBTN.drawButton(false);
  okBTN.drawButton(false);
}

void initProcessScreen() {
  tft.fillRect(0, 0, 480, 320, BLACK);
  tft.drawRoundRect(3, 2, 474, 120, 10, WHITE);
  
  tft.setTextSize(TEXTSIZESMALL);
  tft.setTextColor(WHITE);
  for(int i=0; i<5; i++) {
    tft.setCursor(10, 140+i*30+TEXTOFFSET);
    tft.print(processscreen[i]);
  }
}

void initFinishScreen() {
  //delete keyboard, keep the rest
  tft.fillRect(3, 122, 474, 152, BLACK);

  tft.setTextSize(TEXTSIZESMALL);
  tft.setTextColor(WHITE);
  for(int i=0; i<5; i++) {
    tft.setCursor(10, 140+i*30+TEXTOFFSET);
    tft.print(finishscreen[i]);
  }

  backBTN.drawButton(false);
  okBTN.drawButton(false);
}

void initConfirmationScreen() {
  //delete keyboard, keep the rest
  tft.fillRect(3, 122, 474, 152, BLACK);

  tft.setTextSize(TEXTSIZESMALL);
  tft.setTextColor(RED);
  for(int i=0; i<5; i++) {
    tft.setCursor(10, 140+i*30+TEXTOFFSET);
    tft.print(confirmationscreen[i]);
  }

  tft.setTextColor(WHITE);
  backBTN.drawButton(false);
  okBTN.drawButton(false);
}

void initExternalControlScreen() {
  //delete keyboard, keep the rest
  tft.fillRect(0,0, 480, 320, BLACK);

  tft.setTextSize(TEXTSIZESMALL);
  tft.setTextColor(RED);
  for(int i=0; i<5; i++) {
    tft.setCursor(10, 140+i*30+TEXTOFFSET);
    tft.print(externalscreen[i]);
  }
}

void drawImageArea() {
  if (imgIndex == 0) {
    tft.fillRoundRect(93, 6, 70, 112, 10, BLACK);
    tft.setTextColor(GREY);
    tft.setTextSize(TEXTSIZESMALL);
    tft.setCursor(95, 20+TEXTOFFSET);
    tft.print(designtitle[0]);
    tft.setCursor(95, 50+TEXTOFFSET);
    tft.print(designtitle[1]);
    tft.setCursor(95, 80+TEXTOFFSET);
    tft.print(designtitle[2]);
    tft.drawRoundRect(93, 6, 70, 112, 10, GREY);
  } else {
    tft.drawBitmap(93, 10, epd_bitmap_allArray[imgIndex-1], 70, 100, WHITE);
  }
}

void drawTextArea() {
  if(txtIndex == 0) {
    tft.fillRect(163, 6, 300, 112, BLACK);
    tft.setTextColor(GREY);
    tft.setTextSize(TEXTSIZEBIG);
    tft.setCursor(180, 20+TEXTOFFSET);
    tft.print(designtitle[3]);
    tft.setCursor(180, 50+TEXTOFFSET);
    tft.print(designtitle[4]);
    tft.setCursor(180, 80+TEXTOFFSET);
    tft.print(designtitle[5]);
  } else {
    tft.fillRect(163, 6, 300, 112, BLACK);
    tft.setTextColor(WHITE);
    tft.setTextSize(TEXTSIZEBIG);
    int txtOffset = 30;
    if (txtIndex>txtMaxLength) txtOffset = 15;
    if (txtIndex>txtMaxLength*2) txtOffset = 0;
    for (int i = 0; i < txtIndex; i++) {
      tft.setCursor(180 + 18 * (i%txtMaxLength), 20 + 30 * (i/txtMaxLength)+txtOffset+TEXTOFFSET);
      tft.print(keyChar[txtBuf[i]]);
    }
    if (txtIndex<txtMaxLength*3) {
      tft.setTextColor(GREY);
      tft.setCursor(180 + 18 * (txtIndex%txtMaxLength), 20 + 30 * (txtIndex/txtMaxLength)+txtOffset+TEXTOFFSET);
      tft.print("|");
    }
  }
}

// Array of button addresses to behave like a list
TFT_eSPI_Button *keyPadButtons[60];
TFT_eSPI_Button *backButtons[] = {&backBTN, NULL};
TFT_eSPI_Button *okButtons[] = {&okBTN, NULL};
TFT_eSPI_Button *imageButtons[] = {&imageBTN, NULL};

void initKeyPadButtons() {
  for (int i = 0; i < 3; i++) {
    for (int j = 0; j < 10; j++) {
      keyPadButtons[i*10+j] = &keypad[i][j];
    }
  }
  keyPadButtons[30] = NULL;
}

// update the state of a button and redraw
bool update_button(TFT_eSPI_Button *b, bool down) {  
  b->press(down && b->contains(pixel_x, pixel_y));
  if (b->justReleased())
    b->drawButton(false);
  if (b->justPressed())
    b->drawButton(true);
  return down;
}

bool update_button_list(TFT_eSPI_Button **pb) {
  bool down = Touch_getXY();
  //Serial.println("Update Buttons");
  for (int i = 0; pb[i] != NULL; i++) {
    //Serial.println("check button");
    update_button(pb[i], down);
  }
  return down;
}

void loop(void) {
  bool down = Touch_getXY();
  // direct connection through bluetooth for external control
  if (Serial.available()) {
    SerialBT.write(Serial.read());
  }
  //passcode not working, alternative confirmation on screen for first received char
  if (SerialBT.available()) {
    if (BTconfirmed==0){
      initConfirmationScreen();    
      while(BTconfirmed==0) {
        down = Touch_getXY();
        confirmationWindow();
      }
    }
      // show cinfirmation window, set unconfirmed == true}
    if (BTconfirmed==2){
      Serial.write(SerialBT.read());
    }
  }

  if(pageIndex == 0) welcomeBadge();
  if(pageIndex == 1) designBadge();
  if(pageIndex == 2) startBadge();
  if(pageIndex == 3) processBadge();
  if(pageIndex == 4) finishBadge();
}

void confirmationWindow() {
  update_button_list(backButtons);
  if (backBTN.justPressed()) {
    BTconfirmed = 1;
    if(pageIndex == 0) initWelcomeScreen();
    if(pageIndex == 1) initDesignScreen();
    if(pageIndex == 2) initStartScreen();
    if(pageIndex == 3) initProcessScreen();
    if(pageIndex == 4) initFinishScreen();
  }
  update_button_list(okButtons);
  if (okBTN.justPressed()) {
    BTconfirmed = 2;
    pageIndex = 5;
    initExternalControlScreen();
  }
}

void welcomeBadge() {
   update_button_list(okButtons);
  if (okBTN.justPressed()) {
    pageIndex++;
    initDesignScreen();    
  }
}

void designBadge() {
  update_button_list(keyPadButtons);
  for (int i = 0; i < 3; i++) {
    for (int j = 0; j < 10; j++) {
      if(keypad[i][j].justPressed()){
        if (txtIndex < 30) {
          txtBuf[txtIndex] = i*10+j;
          txtIndex++;
          drawTextArea();
        }
      }
    }
  }
  update_button_list(imageButtons);
  if (imageBTN.justReleased()) {
    imgIndex++;
    if(imgIndex>imgNumber) imgIndex=1;
    drawImageArea();
  }
  update_button_list(backButtons);
  if (backBTN.justPressed()) {
    if(txtIndex > 0) {
      txtIndex--;
      drawTextArea();
    }
  }
  update_button_list(okButtons);
  if (okBTN.justPressed()) {
    pageIndex++;
    initStartScreen();
  }
}

//scanne array, hex zu bit, position mitzählen, je pixel+1, daraus x,y Koordinaten (%Breite, /Höhe)
// ggfs fallunterschiedung hex oder direkt in binär wandeln
// 0x00 -> position+32, nix machen da alles null
// sonst binärwerte durchgehen, wenn ≠1 an position fahren und Pixel ausführen (ggfs mit delay, hoch/runter, laser an/aus), in jedem Fall position +1
//-> abhängig Tool, rest immer gleich

void startBadge() {
  update_button_list(okButtons);
  if (okBTN.justPressed()) {
    pageIndex++;
    initProcessScreen();   
  } 
   update_button_list(backButtons);
  if (backBTN.justPressed()) {
    pageIndex=1;
    tft.fillRect(3, 122, 474, 150, BLACK);
    for (int i = 0; i < 3; i++) {
      for (int j = 0; j < 10; j++) {
        keypad[i][j].drawButton(false);
      }
    }
  }
}
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
////void loop(){
////
////  while(restart){
////    openFileSD();
////    sendGcode();
////  }
////}
//
////change fo file numbers
//void openFileSD(){
//
//  String fileName = "";
//  char fileNameChar[100]={0};       // char array for SD functions arguments
//
//  Serial.println("Enter name for a gcode file on SD : \n");
//  emptySerialBuf(0);
//  fileName=getSerial(0);
//
//  for(int i=0;fileName.charAt(i)!='\n';i++)   //convert String in char array removing '\n'
//    fileNameChar[i]=fileName.charAt(i);
//
//  if(!SD.exists(fileNameChar)){       //check if file already exists
//    Serial.print("-- ");
//    Serial.print(fileNameChar);
//    Serial.print(" doesn't exists");
//    Serial.println(" --");
//    Serial.println("Please select another file\n");
//        delay(200);
//        openFileSD();
//    } 
//    else{
//      myFile = SD.open(fileNameChar, FILE_READ);    //create a new file
//      Serial.print("-- ");
//      Serial.print("File : ");
//    Serial.print(fileNameChar);
//    Serial.print(" opened!");
//    Serial.println(" --\n");
//    }
//}
//
//void emptySerialBuf(int serialNum){
//  //Empty Serial buffer
//  if(serialNum==0){
//    while(Serial.available())                      
//      Serial.read();
//  }
//  else if(serialNum==1){
//    while(Serial1.available())                      
//      Serial1.read();
//    }
//}
//
//void waitSerial(int serialNum){
//  // Wait for data on Serial
//  //Argument serialNum for Serial number
//
//  boolean serialAv = false;
//
//  if(serialNum==0){
//    while(!serialAv){ 
//      if(Serial.available())
//        serialAv=true;
//    }
//  }
//  else if(serialNum==1){
//    while(!serialAv){ 
//      if(Serial1.available())
//      serialAv=true;
//    }
//  }
//}
//
//String getSerial(int serialNum){
//
//  //Return String  from serial line reading
//  //Argument serialNum for Serial number
//
//  String inLine = "";
//  waitSerial(serialNum);
//
//  if(serialNum==0){
//    while(Serial.available()){              
//      inLine += (char)Serial.read();
//      delay(2);
//    }
//    return inLine;
//  }
//  else if(serialNum==1){
//    while(Serial1.available()){               
//        inLine += (char)Serial1.read();
//        delay(2);
//    }
//    return inLine;
//  }
//}
//
//void sendGcode(){
//
//  //READING GCODE FILE AND SEND ON SERIAL PORT TO GRBL
//
//  //START GCODE SENDING PROTOCOL ON SERIAL 1
//
//  String line = "";
//
//    Serial1.print("\r\n\r\n");      //Wake up grbl
//    delay(2);
//    emptySerialBuf(1);
//    if(myFile){                                                                      
//      while(myFile.available()){    //until the file's end
//        line = readLine(myFile);  //read line in gcode file 
//          Serial.print(line);   //send to serials
//          Serial1.print(line);
//          Serial.print(getSerial(1)); //print grbl return on serial
//    }
//  }
//  else
//    fileError();
//
//  myFile.close();
//  Serial.println("Finish!!\n");
//  delay(2000);
//}
//
//void fileError(){
//
//  // For file open or read error
//
//  Serial.println("\n");
//  Serial.println("File Error !");
//}
//
//String readLine(File f){
//  
//  //return line from file reading
//  
//  char inChar;
//  String line = "";
//
//  do{
//    inChar =(char)f.read();
//      line += inChar;
//    }while(inChar != '\n');
//
//  return line;
//}

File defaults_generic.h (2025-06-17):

/*
  defaults_generic.h - defaults settings configuration file
  Part of Grbl

  Copyright (c) 2012-2015 Sungeun K. Jeon

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
  You should have received a copy of the GNU General Public License
  along with Grbl.  If not, see <http://www.gnu.org/licenses/>.
*/

/* The defaults.h file serves as a central default settings file for different machine
   types, from DIY CNC mills to CNC conversions of off-the-shelf machines. The settings
   here are supplied by users, so your results may vary. However, this should give you
   a good starting point as you get to know your machine and tweak the settings for your
   nefarious needs. */

#ifndef defaults_h
#define defaults_h

  // Grbl generic default settings. Should work across different machines.
  #define DEFAULT_X_STEPS_PER_MM 460.0
  #define DEFAULT_Y_STEPS_PER_MM 460.0
  #define DEFAULT_Z_STEPS_PER_MM 460.0
  #define DEFAULT_X_MAX_RATE 460.0 // mm/min
  #define DEFAULT_Y_MAX_RATE 460.0 // mm/min
  #define DEFAULT_Z_MAX_RATE 460.0 // mm/min
  #define DEFAULT_X_ACCELERATION 50 // 10*60*60 mm/min^2 = 10 mm/sec^2
  #define DEFAULT_Y_ACCELERATION 50 // 10*60*60 mm/min^2 = 10 mm/sec^2
  #define DEFAULT_Z_ACCELERATION 50 // 10*60*60 mm/min^2 = 10 mm/sec^2
  #define DEFAULT_X_MAX_TRAVEL 69 // mm
  #define DEFAULT_Y_MAX_TRAVEL 63 // mm
  #define DEFAULT_Z_MAX_TRAVEL 20 // mm
  #define DEFAULT_STEP_PULSE_MICROSECONDS 10
  #define DEFAULT_STEPPING_INVERT_MASK 0
  #define DEFAULT_DIRECTION_INVERT_MASK 0
  #define DEFAULT_STEPPER_IDLE_LOCK_TIME 25 // msec (0-254, 255 keeps steppers enabled)
  #define DEFAULT_STATUS_REPORT_MASK ((BITFLAG_RT_STATUS_MACHINE_POSITION)|(BITFLAG_RT_STATUS_WORK_POSITION))
  #define DEFAULT_JUNCTION_DEVIATION 0.01 // mm
  #define DEFAULT_ARC_TOLERANCE 0.002 // mm
  #define DEFAULT_REPORT_INCHES 0 // false
  #define DEFAULT_INVERT_ST_ENABLE 0 // false
  #define DEFAULT_INVERT_LIMIT_PINS 0 // false
  #define DEFAULT_SOFT_LIMIT_ENABLE 1 // false
  #define DEFAULT_HARD_LIMIT_ENABLE 1  // false
  #define DEFAULT_HOMING_ENABLE 1  // false
  #define DEFAULT_HOMING_DIR_MASK 6 // move positive dir
  #define DEFAULT_HOMING_FEED_RATE 50.0 // mm/min
  #define DEFAULT_HOMING_SEEK_RATE 50.0 // mm/min
  #define DEFAULT_HOMING_DEBOUNCE_DELAY 250 // msec (0-65k)
  #define DEFAULT_HOMING_PULLOFF 1.0 // mm

#endif

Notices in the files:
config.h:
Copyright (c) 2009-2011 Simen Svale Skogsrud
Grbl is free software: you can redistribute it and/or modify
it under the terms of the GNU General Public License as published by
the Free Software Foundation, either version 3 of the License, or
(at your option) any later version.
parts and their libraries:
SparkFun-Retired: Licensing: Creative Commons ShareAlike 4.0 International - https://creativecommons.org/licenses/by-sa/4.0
